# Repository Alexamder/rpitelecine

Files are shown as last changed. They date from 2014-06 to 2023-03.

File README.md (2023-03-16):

# RPi Telecine Project

This project consists of code and models for an 8mm film scanner project based around a Raspberry Pi model B and camera module.
Most of the code is written in Python.

The project is designed to be able to reliably capture each frame of a reel of 8mm film 
(Super 8 or Standard 8) as a high quality photo. Bracketing is possible to cope with underexposed
or dense film.

Once captured, the folder of image files can be transferred to a PC for further processing.

Futher information is available in this Github repository:

* [Description of the electronics](docs/electronics.md)
* [Construction details](docs/mechanics.md)
* [Typical workflow used to digitise films](docs/workflow.md)
* [Hints for post production on a PC](post-production/README.md)
* [Detailed photos available in the images folder](images/)

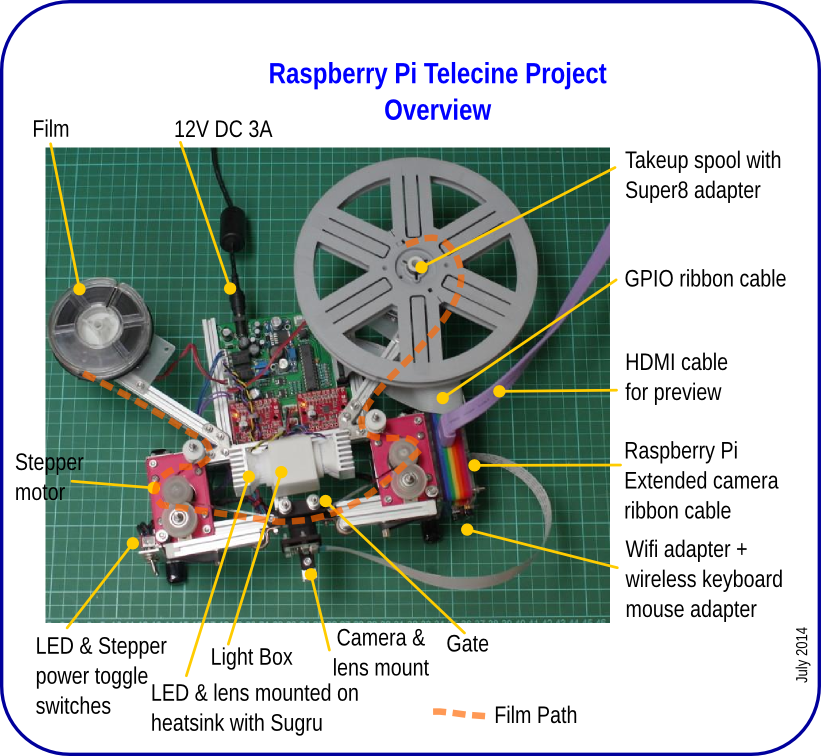
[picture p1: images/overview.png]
Overview of RPI telecine


## Acknowledgements

Thanks to [Raspberry Pi](http://raspberrypi.org) for a splendid little computer and excellent camera module!

Rpi Telecine project design was somewhat inspired by the [Kinograph project](http://kinograph.cc/)

3d printed Gate was inspired [by this design](http://www.mets-telecinesystem.co.uk/index.php/how-its-made/making-the-film-gate).

Chassis makes use of [Makerbeam and accessories](http://www.makerbeam.eu/)

Code makes use of:

* Dave Hughes' [Python picamera library](https://pypi.python.org/pypi/picamera)
* [OpenCV Python bindings](http://opencv.org/)
* Numpy and Scipy

This is a work in progress, and hasn't yet been used on any precious films. It's a good idea to
test using only 'disposable films'. Ebay is a good source of old 'home movies'.

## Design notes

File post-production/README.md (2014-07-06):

# Post-production

These are some simple scripts and snippets of code designed to be run on a full 
power PC, as the Raspberry Pi's ARM processor really isn't up to the job of 
transcoding and processing the large number of images into video. 

My PC runs OpenSUSE Linux with an i5 Processor, and some of the routines take a 
long time.

There are lots of potential processing options, using Linux, OSX or Windows. 
On Linux Openshot and Kdenlive are very good video editors.

## Getting the images onto the PC

Copy the files to from the Pi to the PC. 50 feet of film generates about 5-6GB 
of png files, so it's probably quicker to shut down the Pi, remove the SD card, and
copy the files using an SD card reader on the host PC.  If time isn't an issue, or
you want to keep the Pi running, it's possible to use scp to copy the files over.
As the pictures are stored on the SD card which uses the Ext4 filesystem, you won't be
able to read the card directly on a Windows system without loading additional software.

## Copy files using scp

From the PC, in a terminal:  

```
mkdir <jobname>
cd <jobname>
scp pi@<IP address of Pi>:/home/pi/rpitelecine/<jobname>/*png
```

Replace the job name with the one you chose, and the IP address of the Pi on your 
network. This of course assumes you have set up the ssh server on your Pi. It is possible
to get a work-in-progress copy while the telecine is running a job, but while the
copy is running, the speed of the telecine job halves.

The scp line would be something like:

```
scp pi@192.168.0.13:/home/pi/rpitelecine/familyfilm1/*png
```

With the Pi set up wirelessly, each image takes a second or so to copy. It is quicker to copy 
from the SD card directly, if you are running Linux on the PC. Bear in
mind you are copying about 3,500 pictures for a 50 foot reel of film.

## Create an MP4 film of the video using mencoder

A quick and dirty way of getting video from all the pictures is to use mencoder on
the command line. It's part of mplayer, and should be installed when you installed that
program. I have successfully used this command line:

```
mencoder -nosound -ovc lavc -lavcopts vcodec=mpeg4:mbd=2:trell:autoaspect:vqscale=3 -vf scale=1024:768 -mf type=png:fps=18 mf://img*.png -o <name>.avi
```

Replace <name> at the end with the name of the video you want to create.
You may also want to adjust the framerate after the =fps option - for Super 8 film it
should be 18 frames per second, for standard 8mm it should be 16. Though you may need to 
adjust. Super 8mm with sound is likely to have been shot at 24fps, and older film may be
shot at slower than 16fps...

Digital video players I have tried on the PC, media player hardware, and youtube doesn't 
seem to have trouble with the odd framerate, so it isn't necessary to interpolate frames, 
or alter the rate unless you wish to output to a media like DVD with a fixed 25fps format.

# Use enfuse for combining bracketed pictures

Enfuse is part of Hugin - and is a command line utility that can combine two or more
pictures of the same scene taken with different exposures. [Details here](http://enblend.sourceforge.net/)

Film has a wider dynamic range than is available with the Raspberry Pi camera, so in 
some circumstances it is useful to take two (or possibly more) picturs of the film frame
in order to get as much detail out of it as possible - this is especially true with underexposed
film, or in scenes with a lot of shadow. Some scenes benefit more than others with this
processing, so it may be better to process the normal exmposures as well, and combine
the best scenes using a video editor.

Enfuse can be used to simply combine bracketed sequences pictures using this Python script:

```python
import glob
import os
import subprocess

brackets = 2
name_template = 'img-?????-?'
fmt = '.png'
out_prefix = 'frame-'

files=sorted(glob.glob(name_template + fmt))
n_frames =  len(files)/brackets
FNULL = open(os.devnull, 'w')

processes = 4	# Optimise for number of cores - 4 works well on my i5
counter = 0
while files:
    frame1 = files.pop(0)
    frame2 = files.pop(0)
    outfile = out_prefix + frame1[4:9] + fmt
    print('{}+{} -> {}'.format(frame1,frame2,outfile))
    counter += 1
    cmd = ['enfuse', '-v0', frame1, frame2, '-o', outfile ]
    if counter % processes == 0:
        # Wait until this one finishes
        subprocess.call( cmd, stdout=FNULL, stderr=subprocess.STDOUT)
    else:
        # run in background
        subprocess.Popen( cmd, stdout=FNULL, stderr=subprocess.STDOUT )
```
It very simply goes through all the frames in a sequence, and combines pairs with matching
sequence numbers, creating a new sequence. Enfuse runs slowly, about 1 a second even on my 
Core i5 - but as it only uses a single core on the processor, this script backgrounds 3 of every four, so in
effect running four times faster than simply doing one at a time.

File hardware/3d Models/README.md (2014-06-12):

RPi Telecine Project 3D Models
==============================

These models were created using Freecad parametric design, using v0.14
unstable version. http://freecadweb.org/

STL files were exported and printed using [Shapeways](http://www.shapeways.com/) and 
[3dPrintuk](http://www.3dprint-uk.co.uk/). Film transport rollers were printed using
Shapeways' frosted detail plastic. Seems to work better than Nylon. The gate and camera
mount were printed using Shapeways black nylon. Other parts were standard white nylon.

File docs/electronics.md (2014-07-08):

# RPi Telecine Electronics

## The PCB

The PCB design is pretty simple and comprises the following sections:

* 12V input
* Connectors for 5V regulator for Raspberry Pi and DC motors
* MCP23S17 12 bit IO chip connected to Raspberry Pi SPI port
* 2 x XPPower LED Driver modules + filter and control voltage circuitry
* Headers for 2 x Big Easy Driver stepper motor controllers
* Optically isolated shutter release for external camera
* Mosfet switches for power to 2 x DC motors + LED light
* 5 x GPIO header for unused bits on MCP23S17
* Headers for toggle switches for power to LEDs + Stepper motors
* Headers for 2x power LEDs, 2x DC motors, 2x 4wire stepper motors
* 26way header for Raspberry Pi GPIO port

The PCB is 10cm x 10cm, and is designed to connect to the Pi with a ribbon 
cable. It might be possible to connect it directly to the Pi - but a spacer 
may be required to clear the Pi's ethernet port, and allow space for the camera 
ribbon cable.

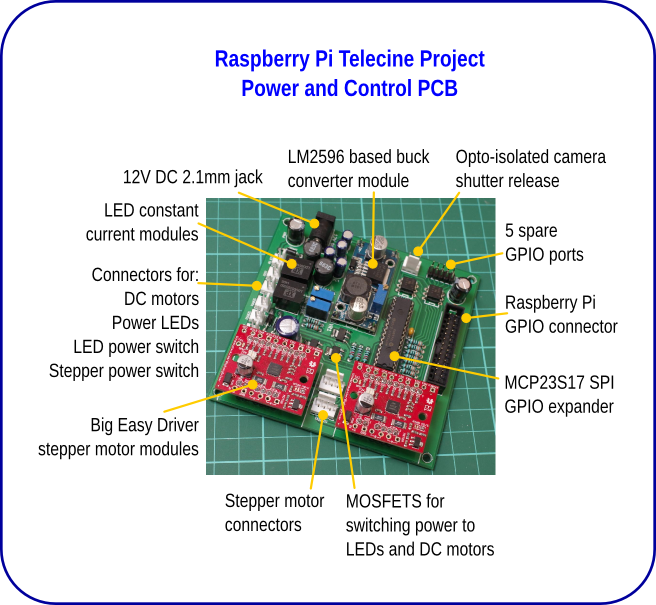
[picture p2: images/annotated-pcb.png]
PCB overview


It is a pretty simple circuit - all through hole components, except for three 
power Mosfets. It uses modules for the 5V power regulator, LED drivers, and 
stepper motors. Power is designed to be provided by a 12V supply, rated at 3A+,
that uses a standard 2.1mm DC jack plug.

5V is provided by an inexpensive LM2596 based module, soldered to headers on 
the PCB. It's also possible to use an alternative buck converter using the pads 
for an alternative header. It's important to use a module that can cope with 2A 
output. I found one of the two LM2596 modules I bought dropped the voltage too 
much when the DC motors were powered, causing the Pi to reboot. Not good. The 
other one works fine. On the prototype I also used a hacked 2A rated car-USB
adapter.

The Raspberry Pi is powered through the 5V line on the 26way connector, so as 
this avoiding the protection on the Pi, it is very important to check the 
voltage provided by the regulator so that it exactly outputs 5V. These modules 
can be set to output anything from 1 - 12V. Adjust the trimmer to the correct 
voltage before connecting the Pi.

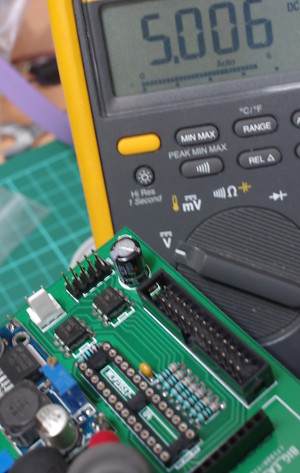
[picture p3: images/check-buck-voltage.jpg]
Check for 5V out of the regulator!

**Very Important**

Using a SPI controlled 16 bit IO expander (the MCP23S17) means that everything 
can be controlled simply using the Python bindings for 
[WiringPi](http://pi.gadgetoid.com/article/wiringpi-version-2-with-extra-python).
It also means that the telecine control scripts can be run as a normal user.

LEDs take advantage of XPPower's LDU05/07/14 Series constant current 
drivers. I have tested with their 700mA, 350mA versions. Details and a link to the 
datasheet are available 
[here](http://uk.farnell.com/xp-power/ldu0516s350/led-driver-dc-dc-cc-0-35a-14v/dp/2082733).
[Datasheet PDF](http://www.xppower.com/pdfs/SF_LDU05-14.pdf) The input filter 
using a 68uH inductor is from the datasheet. The inductors are also available 
[from Farnell](http://uk.farnell.com/murata-power-solutions/13r683c/inductor-68uh-10-1-3a-th-radial/dp/2062695)

The LED drivers also allow for brightness adjustment using a voltage control. I 
implemented this using a trimmer potentiometer and voltage divider.

Stepper motor drivers are 
[Big Easy Stepper drivers](http://www.schmalzhaus.com/BigEasyDriver/) available from 
[Pimoroni](http://shop.pimoroni.com/products/sparkfun-big-easy-driver), 
[Hobbytronics](http://www.hobbytronics.co.uk/big-easy-stepper-driver),
[Sparkfun](https://www.sparkfun.com/products/11876) and other places. They're 
really easy to use, and support 1/16th microstepping, which allows for fine tuning 
of the position of the film. The drivers are plugged into header sockets on the
PCB. It's possible to use screw terminals on the BED boards, or use 2.54mm headers
for the motors. As the BigEasyDriver boards are controlled by 3.3V logic, the 3V/5V 
jumper pad has to be bridged with solder.

Mosfets on the board are the only surface mount components - these are in 
SOT-223 format which is pretty easy to solder. IRLL024NPBF.
[From farnell](http://uk.farnell.com/international-rectifier/irll024npbf/mosfet-n-55v-4-4a-sot-223/dp/8651205?Ntt=8651205)
or cheaper [from CPC](http://cpc.farnell.com/jsp/search/productdetail.jsp?SKU=SC11049) 
These switch the power to the DC motors and for the LED modules. These are logic level
MOSFETS, and are rated to 55V and 4.4A, and require only 2.2V to switch on fully.

Camera release is based around a pair of 4N35 optocouplers. With a 2.5mm jack it can
be used for Canon and Pentax DSLRs. Might also be suitable for other cameras. The 
optocouplers isolate the camera circuit from the Pi. This isn't used for my current
project, but means the PCB is versatile, so could be used with an DSLR like the 
original Kinograph system - or allows the PCB to be used as a timelapse controller.

PCB was designed in Kicad, and I created modules and footprints for the 
BigEasyDrivers, LED drivers and DC module. It was made by Smart-Prototyping, as 
they were having  a special offer on 10x10cm boards.

[Kicad project files are here](../hardware/RPI telecine circuit.zip).

[Gerbers for the PCB are here](../hardware/Gerbers.zip).

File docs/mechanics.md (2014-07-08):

# RPi Telecine construction

## Chassis

The chassis is constructed mainly from [Makerbeam](http://www.makerbeam.eu/) 
10mm extruded aluminium, and associated accessories. The Nema 17 stepper 
motors use the Makerbeam metal bracket, and the servo motors use the lasercut
acrylic servo mount. Arms for the pinch rollers are attached using the
bearing mounts, and the PCB slots between two 10cm beams. The Raspberry Pi in a
Pibow case is attached to the front beam with long steel M3 screws in place
of the standard nylon ones. A long camera ribbon cable goes from the Pi to the
camera.

## 3d printed parts

Various parts in the telecine were 3d printed. A fair amount of precision is required for the 
film handling. It's important that the film path is pretty level - from film-spool to motor 
to gate to motor to take-up spool. 
[Shapeways](http://www.shapeways.com/) and [3dPrintUK](http://www.3dprint-uk.co.uk/)
were used. Shapeways offer a variety of materials and colours, and 3dPrintUK are slightly 
faster and cheaper for larger items - but only in white nylon.

Parts were designed in [Freecad](http://freecadweb.org/), and STL files were sent to
the 3d printing service. Freecad allows designs to be made based on cross-sectional
drawings, and results have been very good.

* Film Gate
* Pi camera mount
* Film roller on stepper motor
* Pinch roller
* Film Idler rollers
* Spool tables
* Light box
* Makerbeam end-stop (protects rubber band)

The film rollers and pinch rollers were printed in Shapeways' frosted detail plastic,
as this gives a good smooth surface for gripping the film edges. First version in 
white standard nylon slipped more. The pinch rollers use bearing races so they can rotate
freely. The film rollers fit steppers with a 5mm D shaped shaft. A little bit of electrical 
tape was used on the shaft to make a tight fit.

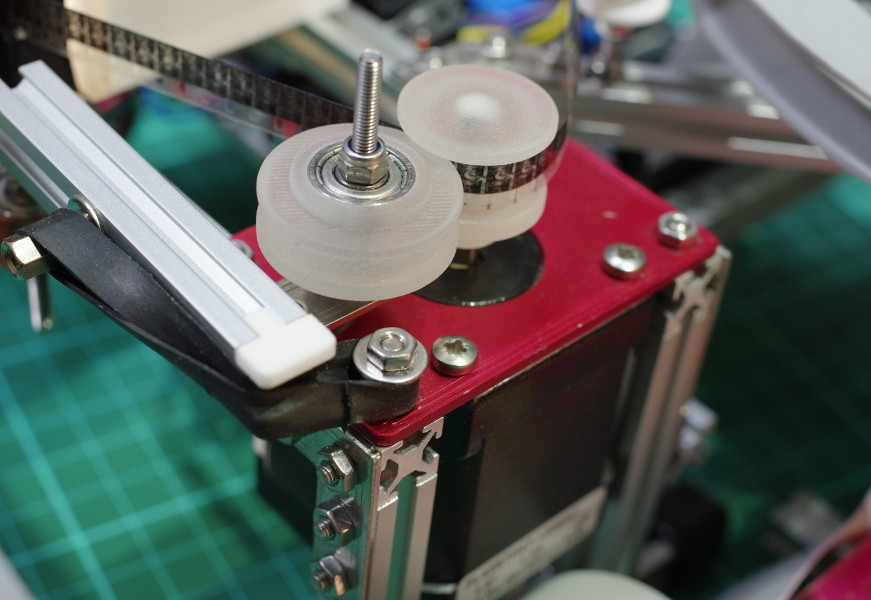
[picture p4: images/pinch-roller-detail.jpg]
Pinch roller detail


Pinch rollers are mounted on swinging arms, and use rubber bands made from an old bicycle 
inner tube to hold the roller in tension with the motor mounted (capstan) roller.
The arms can be released in order to remove the film.

The light box serves to mix the colours of the white and turquoise LEDs, and to diffuse the
light to create a flat area of illumination behind the gate.
The gate and camera mount fit into the slots on the Makerbeam - allowing adustment while
keeping alignment straight.

[Original 3d models and STL files are here](../hardware/3d Models/).

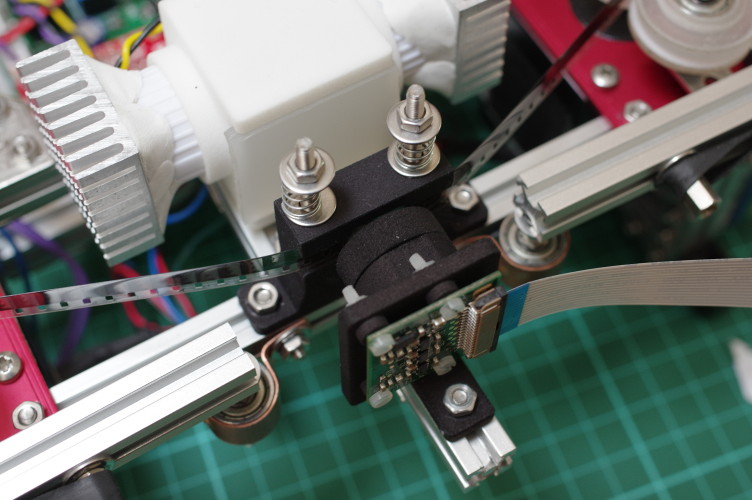
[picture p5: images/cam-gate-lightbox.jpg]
Camera gate and lightbox - 3d printed

3d printed lightbox, gate and camera/lens-mount in situ

## Hacked servos

The film spool tables are attached directly to the splines of the servos. The servos
are standard inexpensive TowerPro MG995s (or copies), but modded for continuous
rotation by pulling out a metal pin that stops the gears rotating 360 degrees, and 
removing the feedback potentiometer. The control PCB was also removed, and two wires
soldered directly to the motor - effectively turning the servo into a compact
simple geared motor. There are various instructions dotted around the net for this
process.

The advantage of using servos is the simplicity of attaching the spool table - it just
uses a single m3 screw, and holds extremely securely. However any DC motor would be suitable.
Film spools are not fixed on the tables - they are designed to rotate freely so film can
be pulled off the reel, and the take-up spool rotates with a little bit of friction, rotating
enough to take up the slack. The motors are designed just to rotate in one direction - in order 
to pull the film onto the spool. 

## Camera and Lens

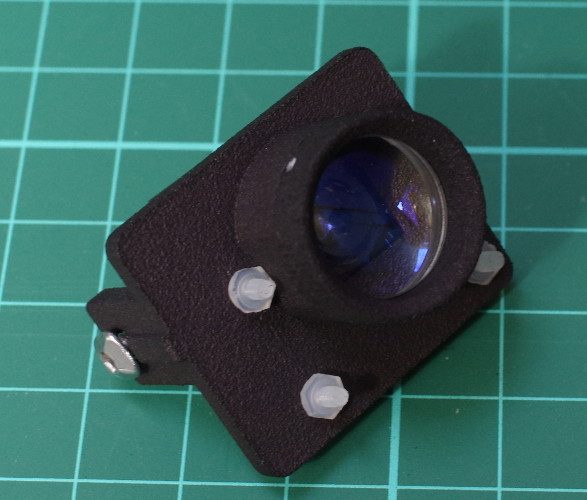
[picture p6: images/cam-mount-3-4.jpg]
Camera and lens assembly


The camera is screwed onto a 3d printed bracket which fits into the slot in a short piece of Makerbeam.
It can be fixed securely, but allows for adjustment and focusing the image. 
To focus closer the Raspberry Pi camera's lens needs to be carefully unscrewed almost
as far as it can. This is not enough to get an 8mm frame large enough in the frame, so an additional
lens is required. 

The first version of the camera mount allowed fixing of a simple
(and inexpensive) smartphone close-up/macro lens. These can be got for cheap from Ebay.
Results using this lens was just about acceptable - the centre of the frame was
pretty sharp, but got softer away from the centre with a fair amount of colour fringing. My 
first examples on Youtube use this lens. Not bad for a lens that costs less than a fiver.

Much better is its replacement - a coated Steinheil triplet, available for a reasonable price from
[Surplus Shed](http://www.surplusshed.com/pages/item/pl1033.html) in the USA. This lens is much sharper
with little chromatic abberation and has less distortion than the smartphone lens. 
It was suggested for macro use by rkinch [in this thread on the Pi forums](http://www.raspberrypi.org/forums/viewtopic.php?f=43&t=43985&start=52).
The camera mount design was adjusted for this lens.

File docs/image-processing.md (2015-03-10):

#Capturing flow

##Image capture

The Pi camera takes a full 5MP image and returns a BGR 8bit image
as an OpenCV compatible Numpy array. A full image capture takes about
0.7 seconds before the data is available. 

##Perforation detection

Perforation detection uses a region of interest - a small part of the whole image
in one channel in order to minimise the amount of processing required.

The perforation will be the largest, brightest area in the ROI image. A vertical 
slice of the ROI is made, and the median value of each row is used to make a 
single column representation of the brightness of the width. This column is
thresholded to create a binary array, and the position of the top and bottom
edge of the perforation is established.

Using a median value across the width of the perforation allows for damaged
sprocket holes. This seems to work quite well.

Optionally the same process is repeated for the left hand edge of the perforation
in order to compensate for horizontal weaving.

The output of the detection is the centre point of the perforation in the image.

##Cropping

The centre point established by the perforation detection is used to calculate
the slice used to crop the film frame from the whole image.

The crop is specified by an offset from the centre point, and its width and 
height. A slice object is created, and the sliced image is sent to the writing
queue.

##Writing

The cut-out frames are placed in a queue with the filename/frame number where 
they are taken by a separate thread and output to SD card or other storage. 
Writing the image data is time consuming. Depending on the size of the image
crop and file format, output is typically 0.8 to 1.5 seconds per frame with
a Raspberry Pi 2 and a reasonably fast Micro-SD card.
 
Using a separate thread to write the images means that the image writing works 
in parallel with moving the film to the next frame, and waiting for the camera
to take the next picture.

##Speed considerations

50 feet of 8mm film has around 3600 frames.
The Pi camera requires 0.7 seconds to set up the camera and take a 5MP still
picture and get the RGB data for further analysis and processing.
The other time consuming process is the saving of the cropped image. A crop that is
about 1800x1300 pixels large takes about 0.9 seconds to write as a 620K JPG, or 
1.4 seconds to write a 3.3MB PNG. 

Experiments have shown that OpenCV is the fastest at saving of images. I have
tried using PIL and Qt, and the PNG save takes in excess of 3-4 seconds. So
it's back to using OpenCV.

Total job time is therefore determined by either the picture taking, or the
image saving elements of the process - whichever is longest.

At present, it doesn't seem possible to increase the speed of the camera. In 
order to get the consistent exposure needed by the telecine, the stills 
port is required. My attemps at trying to get full resolution images using
the Pi's video port have failed. It would be nice to be able to get
multiple images per second out of the camera.

It may be possible to use multiple threads to write the data files - but
this will be limited by the maximum IO speed, either over the USB if 
saving to an external drive, or using the SD card interface. JPEG and PNG
compression require quite a lot of processing power, so it might be beneficial
to have the writing threads on separate processor cores.

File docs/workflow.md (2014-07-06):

# Workflow for a telecine job

This is the basic workflow to convert a film. It's mainly designed for the Pi
to run headless while doing the capture. The setup routine uses a GUI of sorts - 
basically shows a preview of the crop settings, but it is mainly keyboard
controlled.

## Set base exposure

If base whitebalance/shutter speed hasn't been set, or if lighting
has been altered:

1. Without film in gate, put a neutral density filter in front of lamp diffuser
2. Run tc-setwhitebalance.py to set base exposure and white balance

## Set up telecine job

1. Lace the film and pull it through the gate manually. If possible move it to a frame.
2. Run tc-setupjob.py [-b|--brackets] [-s8|--standard8] <jobname>
3. Click in a sprocket hole to set up frame detection
4. Calibrate the transport - press the # key - or do each step individually with u|t|y
5. Use '[' and ']' keys to jump forward or back; or ','/'.' to move one frame forward, back
6. Adjust the crop with arrow keys and PgUp/PgDn
7. Adjust the exposure (+/-) and red/blue gains (rR & bB). Toggle greyscale with g. Toggle clipping with 'c'
8. Use transport keys to move the film to the first frame in the job.
9. Save settings to job ini file with s. To exit without saving use Esc.

The preview can be used to check focus, exposure, etc. It's slow, but just about 
usable over a remote X connection (via ssh).

## Run job

1. Run tc-run.py jobname -s start-frame -e end-frame [-j] [-r] [-b]

'-j' option saves images to jpeg. '-r' runs the transport backwards. '-b' forces bracketing.
Start frame and end frame numbers are inclusive. The tc.run.py runs in the console,
so you can use the screen command to run in the background and headless. 

5 consecutive failures to detect a perforation will stop the job. This is usually at
the end of the reel - or if there's some damage on the film.

All frames will be saved to a sub folder named after the job name. Failed 
perforation detections will be saved as full frames as well as cropped, so they
can be cropped manually if necessary.

## Keys in setup routine

| Keys | Description |
| --- | --- |
| s | Save current settings |
| Esc	 | Escape without saving |
| c	 | Toggle clipped colours |
| g	 | Toggle grayscale |
| d	 | Cycle through DRC settings (off,low,med,high) |
| - +	 | Reduce / increase shutter |
| r  R	 | Reduce / increase red gain |
| b  B	 | Reduce / increase blue gain |
| p	 | Toggle perforation detection |
| o	 | Centre frame |
| i	 | Redetect perforation |
| #	 | Calibrate Transport (same as u/t/y) |
| t  y	 | Calibrate transport forward/backward |
| u	 | Calibrate pixels per motor step |
| .  ,	 | Previous / next frame |
| <  >	 | Back or forwards 18 frames |
| [  ]	 | Fast wind back / forward 18 frames |
| {  }	 | Fast wind back / forward 180 frames |
| Arrows | Move crop |
| PgUp	 | Make crop larger |
| PgDn	 | Make crop smaller |
| Home	 | Nudge motor forward |
| End	 | Nudge motor backward |
| 1-4	 | Display reduction (1 full size, 4 quarter size) |

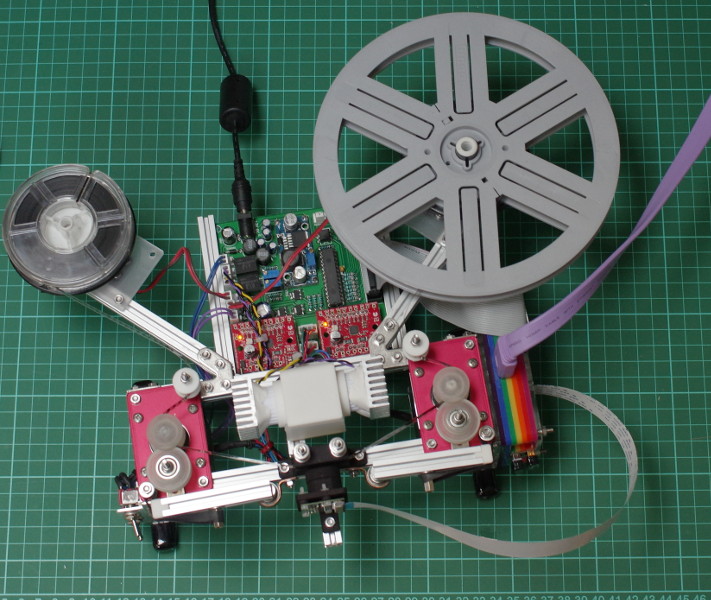
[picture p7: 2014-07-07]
images/rpi-telecine-overview.jpg

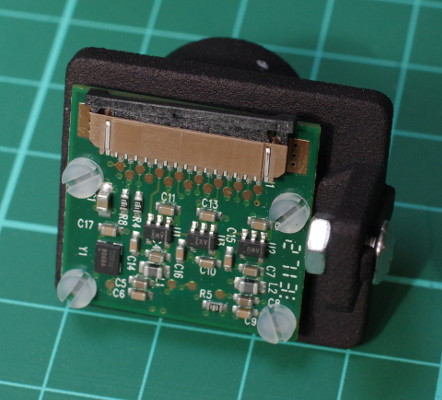
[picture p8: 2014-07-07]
images/cam-mount-3-5.jpg

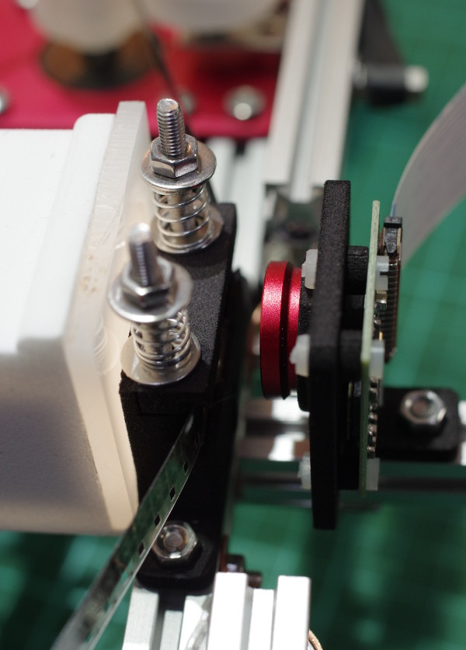
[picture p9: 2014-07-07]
images/orig-lightbox-lens.jpg

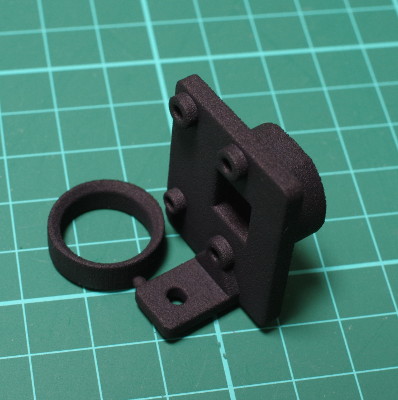
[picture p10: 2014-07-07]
images/cam-mount-3-1.jpg

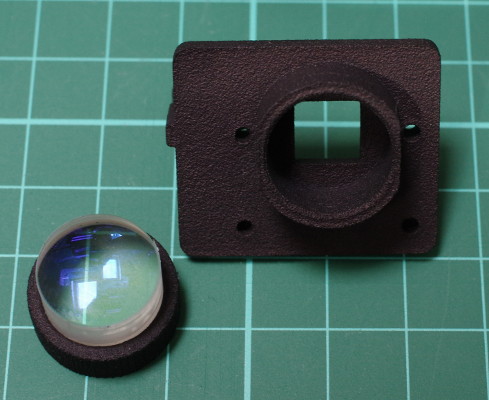
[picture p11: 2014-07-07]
images/cam-mount-3-3.jpg

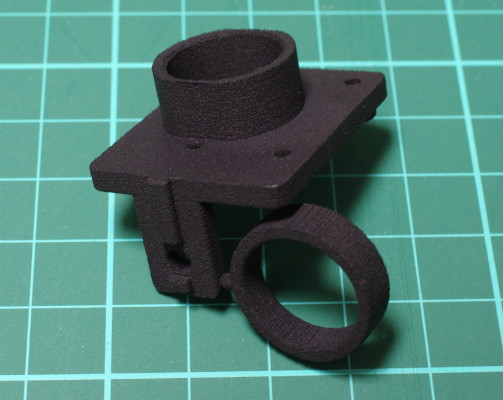
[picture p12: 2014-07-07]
images/cam-mount-3-2.jpg

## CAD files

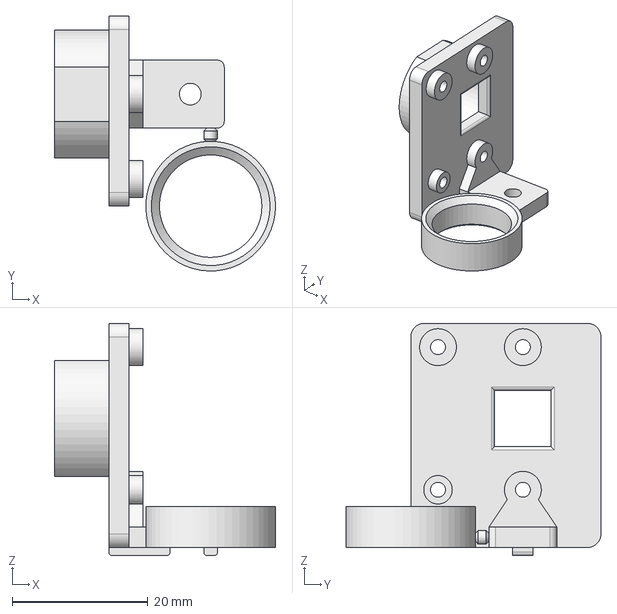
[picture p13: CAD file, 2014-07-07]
hardware/3d Models/camera-mount-3.fcstd
32.6 x 37.5 x 34.2 mm

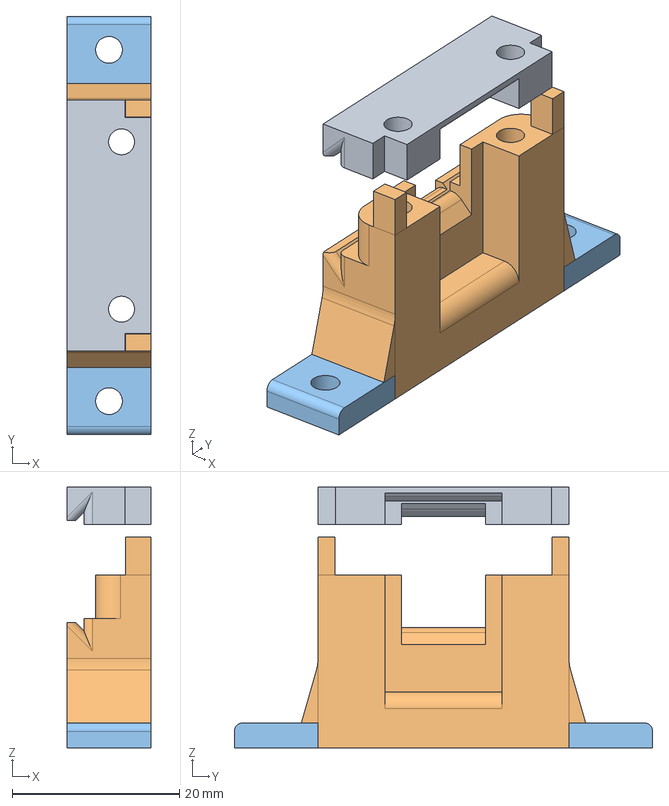
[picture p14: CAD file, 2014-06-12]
hardware/3d Models/gate2.fcstd
10.0 x 50.0 x 31.2 mm

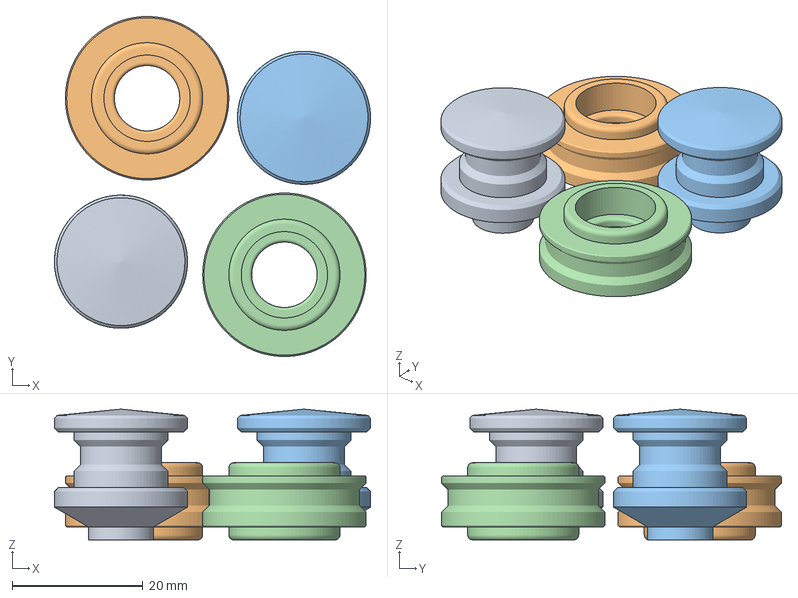
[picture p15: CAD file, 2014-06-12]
hardware/3d Models/rollers-2.fcstd
48.4 x 52.0 x 20.0 mm
motor-roller
pinch-roller
motor-roller001
pinch-roller001

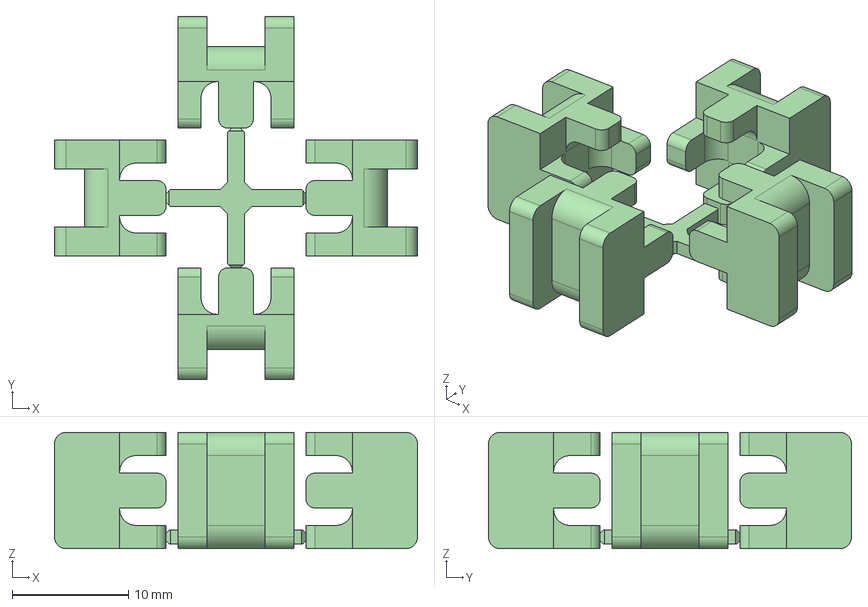
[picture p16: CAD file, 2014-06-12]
hardware/3d Models/beam-stop.fcstd
31.2 x 31.2 x 10.0 mm
Sprue
Fusion Refined

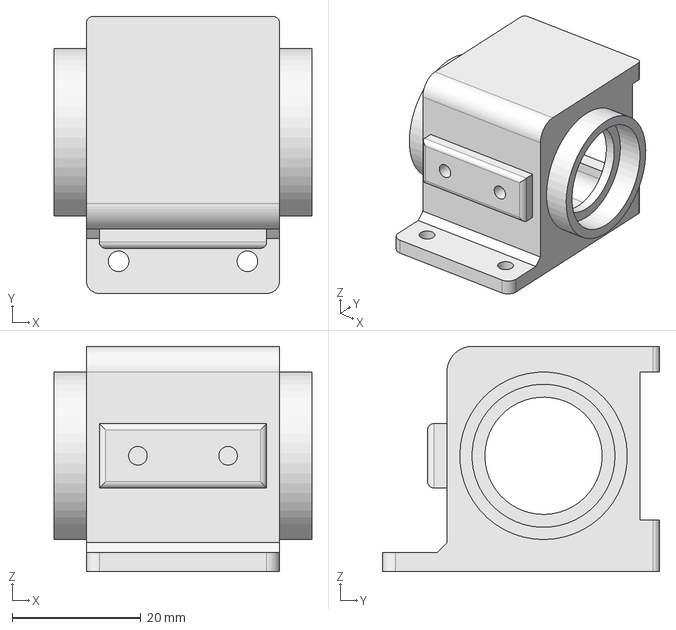
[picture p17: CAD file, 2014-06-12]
hardware/3d Models/lightbox2.fcstd
40.0 x 43.0 x 35.0 mm

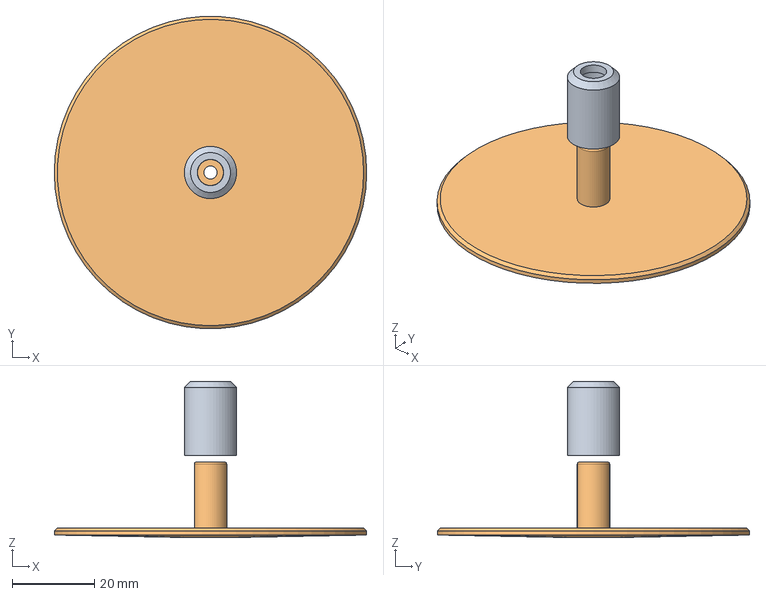
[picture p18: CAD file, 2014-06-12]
hardware/3d Models/film-table.fcstd
75.9 x 75.8 x 38.0 mm
Super8 Adapter
Film Table

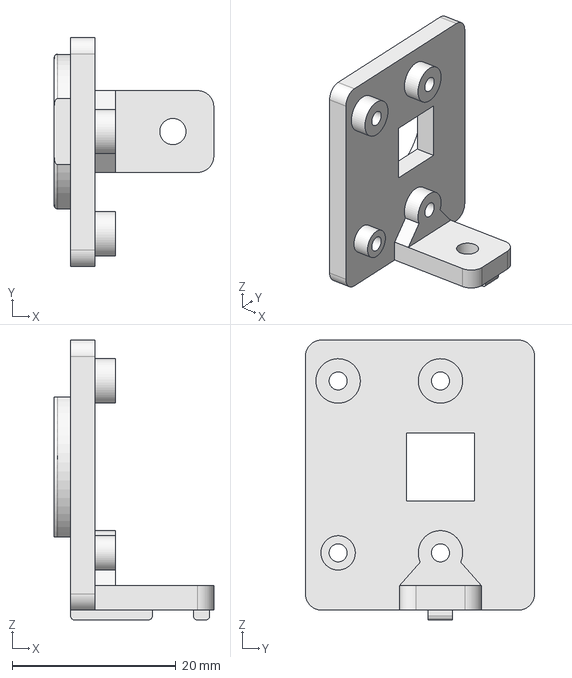
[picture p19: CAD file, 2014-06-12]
hardware/3d Models/camera-mount.fcstd
19.5 x 28.0 x 34.2 mm

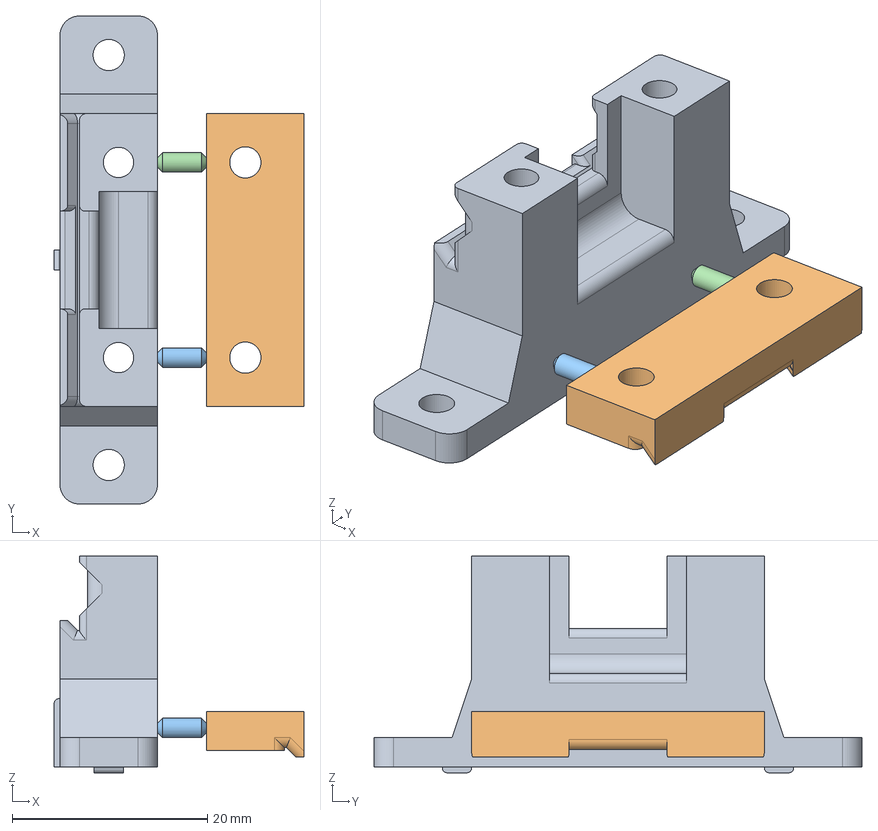
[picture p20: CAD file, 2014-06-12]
hardware/3d Models/gate3.fcstd
25.6 x 50.0 x 22.2 mm
Body001 (Solid)
Top002 (Solid)

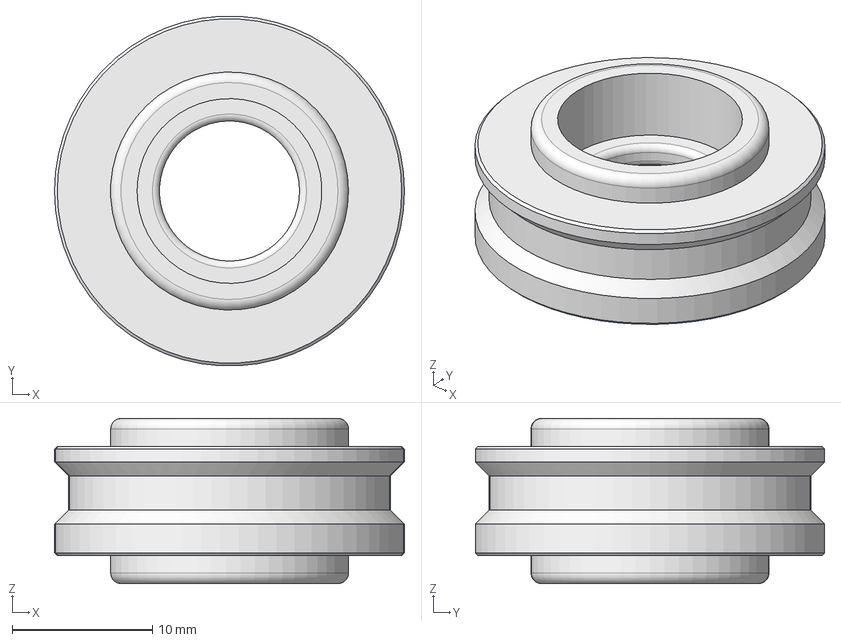
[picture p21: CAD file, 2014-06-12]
hardware/3d Models/pinch-roller.fcstd
25.0 x 25.0 x 11.8 mm

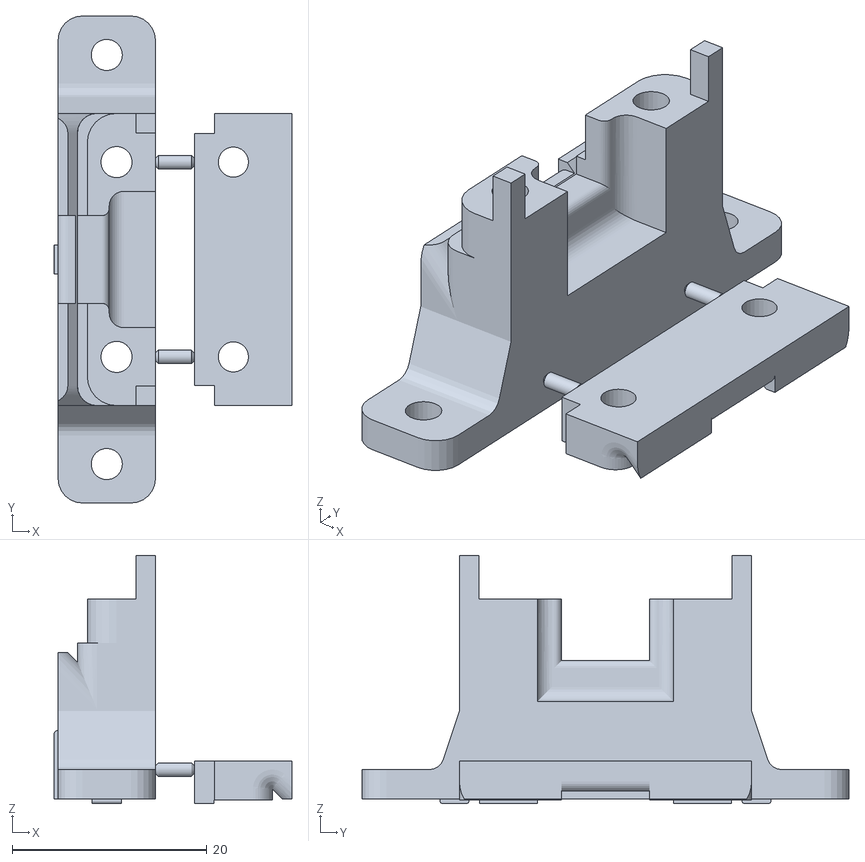
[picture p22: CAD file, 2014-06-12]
hardware/3d Models/gate.stl
24.4 x 50.0 x 25.5

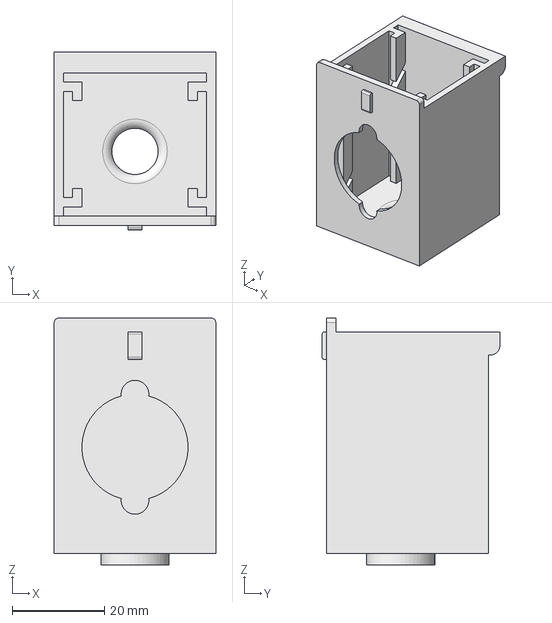
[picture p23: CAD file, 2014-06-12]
hardware/3d Models/light-box.fcstd
35.0 x 38.5 x 53.5 mm

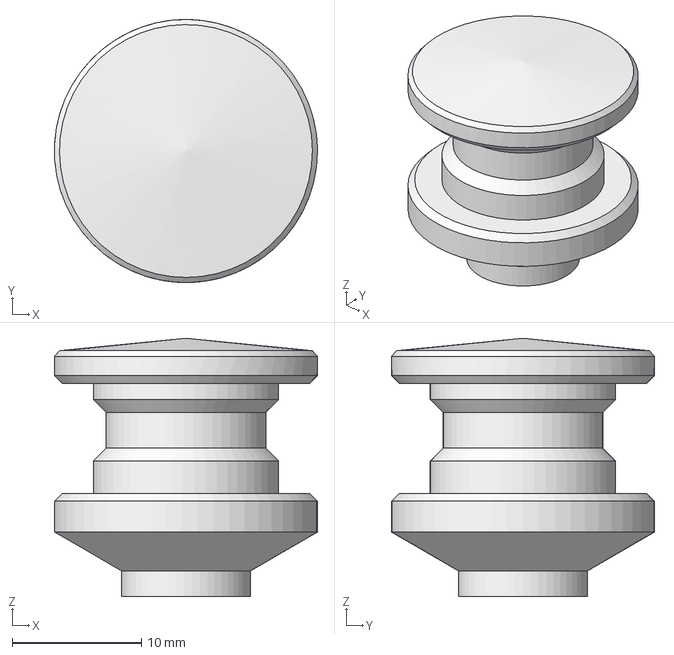
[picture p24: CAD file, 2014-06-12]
hardware/3d Models/motor-roller.fcstd
20.3 x 20.4 x 20.0 mm

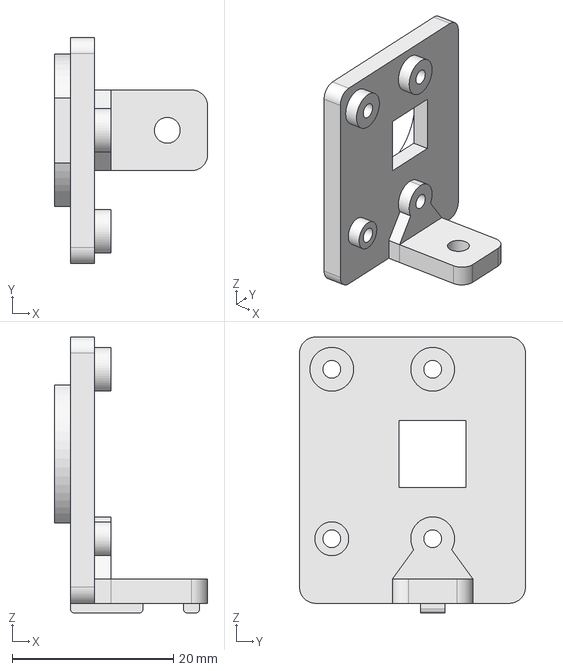
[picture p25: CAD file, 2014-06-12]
hardware/3d Models/camera-mount-2.fcstd
19.0 x 28.0 x 34.2 mm

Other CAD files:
hardware/3d Models/beam-stop.stl
hardware/3d Models/camera-mount2.stl
hardware/3d Models/camera-mount3.stl
hardware/3d Models/gate3.stl
hardware/3d Models/light-box2.stl
hardware/3d Models/rollers2.stl

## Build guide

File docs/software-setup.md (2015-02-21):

# Setting up the rpiTelecine software

These are the steps required to get the Python scripts working with my 
telecine hardware. I am currently using a Raspberry Pi B version 2 - as the telecine 
processing really benefits from additional memory and the extra processor cores.
These instructions were tested using NOOBS 1.4.0 released on 18 February 2015.
A main prerequisite is the Python-picamera library, which is installed by default with
the current version of Raspbian. Other prerequisites are WiringPi2, WiringPi2-Python and OpenCV.

## Download and install NOOBS

Get the latest version from http://www.raspberrypi.org/downloads/
Copy it on a good fast Micro-SD card as per the directions on the Raspberry Pi web site. 
Boot your fresh SD card and install Raspbian.

## raspi-config

When the Pi reboots, various settings are required in raspi-config which runs when the system
starts for the first time. These settings can be done at any time by entering the following at the command line:
```
$ sudo raspi-config
```

* 2 Change user password - it's always a good idea. Make a note of it.
* 5 Enable Camera

The rest of the settings are in the Advanced section:

* A3 Memory Split - Set to 192MB. For full resolution stills, Python picamera requires the GPU to have more RAM than the default
* A4 SSH - Enable SSH if you use SSH to connect to the Pi, or to transfer files from it
* A6 SPI - Enable SPI, and set the kernel module to load by default

Reboot the Pi

## Set up network

Plug in a network cable, or set up the wireless network adapter.
For the latter, the easiest way is to go into LXDE with 'startx' and click Menu->Preferences->WiFi Configuration

## Update and install packages
Python-dev and python-setuptools are used to install wiringPi2; OpenCV is used in the rpiTelecine scripts 
to provide a rudimentary GUI and image saving capability, and Scipy is used for some simple image analysis.

```
$ sudo apt-get update
$ sudo apt-get upgrade
$ sudo apt-get install python-dev python-setuptools 
$ sudo apt-get install libopencv-dev python-opencv python-scipy
```

## Install WiringPi2 and WiringPi2-Python

```
$ git clone git://git.drogon.net/wiringPi
$ cd wiringPi 
$ sudo ./build
$ cd 
$ git clone https://github.com/Gadgetoid/WiringPi2-Python.git
$ cd WiringPi2-Python
$ sudo python setup.py install
$ cd
```

## Install rpiTelecine scripts from Github

```
$ git clone https://github.com/jas8mm/rpiTelecine.git
$ cd rpiTelecine
```

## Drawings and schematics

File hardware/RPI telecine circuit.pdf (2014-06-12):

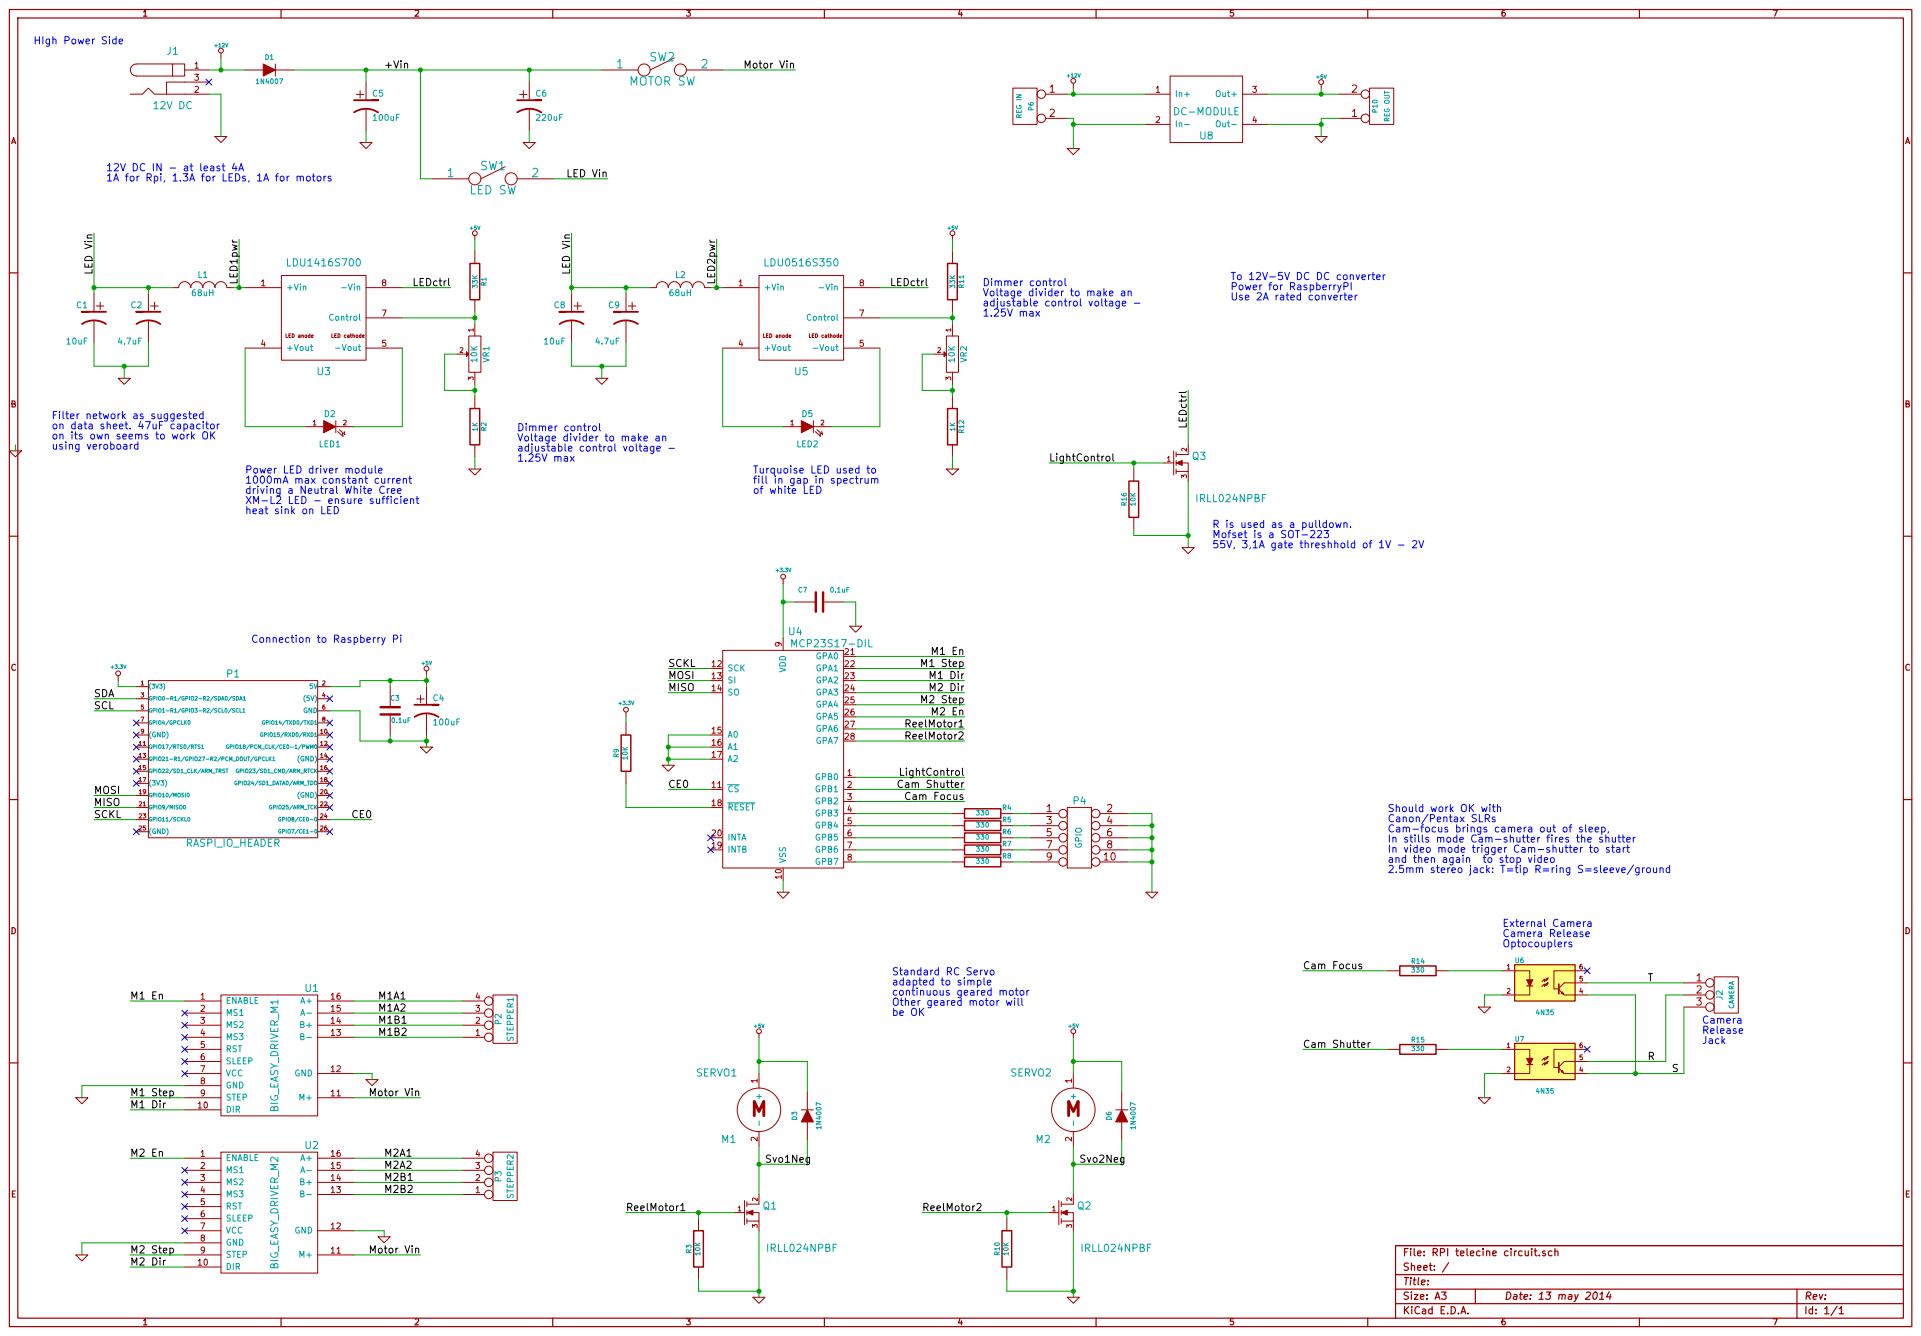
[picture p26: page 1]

+12V M1 Step M1 Dir M1 En M2 En M2 Dir M2 Step

Power for RaspberryPI Use 2A rated converter 12V DC IN - at least 4A
1A for Rpi, 1.3A for LEDs, 1A for motors

To 12V-5V DC DC converter

adjustable control voltage - 1.25V max

adjustable control voltage - 1.25V max Filter network as suggested
on data sheet. 47uF capacitor
on its own seems to work OK

Turquoise LED used to
fill in gap in spectrum
of white LED

1000mA max constant current driving a Neutral White Cree XM-L2 LED - ensure sufficient heat sink on LED

Connection to Raspberry Pi

Jack Should work OK with
Canon/Pentax SLRs
Cam-focus brings camera out of sleep,
In stills mode Cam-shutter fires the shutter
In video mode trigger Cam-shutter to start
and then again to stop video
2.5mm stereo jack: T=tip R=ring S=sleeve/ground

IRLL024NPBF Standard RC Servo
adapted to simple
continuous geared motor
Other geared motor will

Id: 1/1 Title: File: RPI telecine circuit.sch Sheet: /

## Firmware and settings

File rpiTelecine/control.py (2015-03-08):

# RPi Telecine - Controller board 
#
# Code to encapsulate the operation of the controller board
#	
# The telecine board uses an MCP23S17 digital IO expander to control:
# 	2x stepper motors in microstepping mode using  BigEasyDriver modules
# 	2x geared motors for film reel takeup
# 	Power LED to illuminate film
# 	External camera shutter release circuit using 2 opto-couplers.
# 	Remaining pins on the MCP23S17 are broken out for future use and
# 	can be used as GPIOs
# 	
# Version 1 of the PCB is 10x10cm with pin headers for the motors,
# 2 x power LEDs, Raspberry Pi model B and GPIO. Wiringpi2 is used
# for control. The PCB takes a 3A+ 12V power supply, and provides
# power for the Pi using the 5V pin of the Pi's GPIO header.
# For the two power LEDs, XPPower LDU0516S350 (or similar with
# identical pinout) are used. These allow a control voltage to
# adjust the brightness - so they can be trimmed on the board. 
# The PCB uses a LM2596 adjustable buck converter (Check that it
# outputs 5V before connecting the Pi!), and Big Easy Drivers for the
# stepper motors. The BEDs, although expensive, allow the microstepping
# required for the film transport.
# The LED power and DC motors are switched using Mosfets.
#
# Prerequisites: 
#   Wiringpi2 for Python
#   SPI needs to be enabled from raspi-config so the correct kernel 
#   modules are loaded on boot.
#
# Copyright (c) 2014, Jason Lane
# 
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
# 3. Neither the name of the copyright holder nor the names of its contributors 
# may be used to endorse or promote products derived from this software without 
# specific prior written permission.

# THIS SOFTWARE IS PROVIDED BY THE COPYRIGHT HOLDERS AND CONTRIBUTORS "AS IS" AND 
# ANY EXPRESS OR IMPLIED WARRANTIES, INCLUDING, BUT NOT LIMITED TO, THE IMPLIED 
# WARRANTIES OF MERCHANTABILITY AND FITNESS FOR A PARTICULAR PURPOSE ARE 
# DISCLAIMED. IN NO EVENT SHALL THE COPYRIGHT HOLDER OR CONTRIBUTORS BE LIABLE FOR 
# ANY DIRECT, INDIRECT, INCIDENTAL, SPECIAL, EXEMPLARY, OR CONSEQUENTIAL DAMAGES 
# (INCLUDING, BUT NOT LIMITED TO, PROCUREMENT OF SUBSTITUTE GOODS OR SERVICES; 
# LOSS OF USE, DATA, OR PROFITS; OR BUSINESS INTERRUPTION) HOWEVER CAUSED AND ON 
# ANY THEORY OF LIABILITY, WHETHER IN CONTRACT, STRICT LIABILITY, OR TORT 
# (INCLUDING NEGLIGENCE OR OTHERWISE) ARISING IN ANY WAY OUT OF THE USE OF THIS 
# SOFTWARE, EVEN IF ADVISED OF THE POSSIBILITY OF SUCH DAMAGE.


from __future__ import division
from wiringpi2 import *

class tcControl():
    
    pin_base=100
    m1_en_pin = pin_base+0
    m1_step_pin = pin_base+1
    m1_dir_pin = pin_base+2
    m2_en_pin = pin_base+5
    m2_step_pin = pin_base+4
    m2_dir_pin = pin_base+3
    reel1_pin = pin_base+6
    reel2_pin = pin_base+7
    led_pin = pin_base+8
    shutter_pin = pin_base+9
    focus_pin = pin_base+10
    gpio1_pin = pin_base+11
    gpio2_pin = pin_base+12
    gpio3_pin = pin_base+13
    gpio4_pin = pin_base+14
    gpio5_pin = pin_base+15
    
    
    # Parameters to pulse takeup reel every so often to keep film
    # wrapped around rollers
    take_up_steps = take_up_counter = 550
    
    # Because of slippage in system skip pushing film every so often
    # Without this, film tends to start to slacken and bunch up
    # before the gate. 
    tension_steps = 50
    step_counter = 0
    
    def __init__(self):
	wiringPiSetupSys()
	mcp23s17Setup(self.pin_base, 0, 0) 
	# Stepper Motors
	self.m1 = stepperMotor(self.m1_step_pin, self.m1_dir_pin, self.m1_en_pin)
	self.m2 = stepperMotor(self.m2_step_pin, self.m2_dir_pin, self.m2_en_pin)
	# DC motors for takeup reels
	self.reel1 = reelMotor(self.reel1_pin)
	self.reel2 = reelMotor(self.reel2_pin)
	# LED control
	self.led = ledControl(self.led_pin)
	# Shutter release
	self.shutter_release = shutterRelease(self.focus_pin, self.shutter_pin)
	self.m1.on()
	self.m2.on()
	# Direction of film travel - 
	# Forward: True = m1 to m2 False = m2 to m1
	self.m1.set_direction(True)
	self.m2.set_direction(True)
	self.direction = True
	
    def light_on(self):
	self.led.on()
	
    def light_off(self):
	self.led.off()
	
    def change_direction( self, d = True ):
	"""
	Set parameters when direction changes
	"""
	self.direction = d
	self.take_up_counter = self.take_up_steps
	self.step_counter = self.tension_steps
	self.m1.set_direction(d)
	self.m2.set_direction(d)

    def steps_forward(self,steps=1):
	""" 
	Take steps forward - pulse the takeup reel and tension film
	by ignoring push step occasionally
	"""
	m1step = self.m1.step	# Speed up loop a bit by not evaluating dots
	m2step = self.m2.step
        if not self.direction:
            self.change_direction( True )
	while steps>1:
            steps -= 1
	    self.take_up_counter -= 1
            if self.take_up_counter==1:
                self.reel2.pulse()
                self.take_up_counter=self.take_up_steps
	    if self.step_counter>0:
		# Push film one step
		m1step()
		self.step_counter -= 1
	    else:
		# Skip pushing
		self.step_counter = self.tension_steps
	    # Pull film one step
	    m2step()
    
    def steps_back(self,steps=1):
	""" 
	Take steps backwards
	"""
	m1step = self.m1.step	# Speed up loop a bit by not evaluating dots
	m2step = self.m2.step
        if self.direction:
            self.change_direction( False )
        while steps>1:
            steps -= 1
	    self.take_up_counter -= 1
	    if self.take_up_counter==0:
                self.reel1.pulse()
                self.take_up_counter=self.take_up_steps
	    if self.step_counter>0:
		m2step()
		self.step_counter -= 1
	    else:
		self.step_counter = self.tension_steps
	    m1step()	


    def tension_film(self,steps=200):
	# Run steppers in opposite direction for a short period - Tightens up the film
	d = self.direction
	self.m1.set_direction(False)
	self.m2.set_direction(True)	
	for n in xrange(steps):
	    self.m1.step()	
	    self.m2.step()	
	self.m1.set_direction(d)
	self.m2.set_direction(d)

    
    def clean_up(self):
	# Switch things off to tidy up
	self.led.off()
	self.reel1.off()
	self.reel2.off()
	self.m1.off()
	self.m2.off()
	
class stepperMotor():
			
    """
    Simple Stepper motor control class

    Simple class to control stepper motors
    using the BigEasyDriver
    http://www.schmalzhaus.com/BigEasyDriver/

    To control one motor these pins are used:

    EN - Enable/Energise the motor (optional)
    DR - Direction of step
    ST - Step
    GND - Ground connection

    Motor is energised by default - the EN pin can switch power to motor 
    off, to allow manual positioning etc. This connection is optional.

    Big Easy Driver defaults to 3200 steps per rotation, microstepping 
    mode. Re-energising the coils after sleeping will set the nearest 
    whole step
    """

    delay = 1 # Big Easy Driver requires a pulse of 1uS or longer.
    motor_on = False
    
    rotation_steps = 3200
    # Big Easy Driver defaults to 3200 steps per 360degree rotation
    # if the motor has 200 steps per 360degree.
    # Change this if your motor is different
    
    def __init__(self,step_pin,dir_pin,en_pin):
        
        self.step_pin = step_pin
        self.dir_pin = dir_pin
        self.en_pin  = en_pin
        pinMode( step_pin, 1 )         # Output
        pinMode( dir_pin, 1 )          # Output
        pinMode( en_pin, 1 )       	# Output
        self.on()
        self.direction = True
             
    def on(self):
        # enable motor - set motorOn flag
        digitalWrite(self.en_pin,False)
        self.motor_on = True
        
    def off(self):
        # if enable pin is used, de-energise the motor coils
        digitalWrite(self.en_pin,True)
        self.motor_on = False

    def set_direction( self,direction=True ):    
	# set Direction of motor - true=ccw; false=cw
	self.direction = 1 if direction else 0
	digitalWrite(self.dir_pin, self.direction)
        
    def step(self):
	# Make a step
	# Big Easy Driver will step when the pin rises
	# Should be on and off for at least 1uS 
	digitalWrite(self.step_pin,True)
	#delayMicroseconds(self.delay)
	digitalWrite(self.step_pin,False)
	#delayMicroseconds(self.delay)
        
    def steps(self,s):
        # Go s steps
        for i in xrange(0,s):
            self.step()
    
    def rotate_full(self):
        # Make a full rotation
        self.steps(self.rotation_steps)
            
    def rotate_half(self):
        # Make a half rotation
        self.steps(self.rotation_steps//2)
     
    def rotate_quarter(self):
        # Make a quarter rotation
        self.steps(self.rotation_steps//4)

class ledControl:
    """
    Simple Class to control the LED power
    """

    def __init__(self,pin):
	self.pin = pin
	pinMode( pin, True )
	self.off()

    def on(self):
	digitalWrite( self.pin, True )

    def off(self):
	digitalWrite( self.pin, False )


class reelMotor:
    """
	Class to control DC motors for film spools
	The motors are controlled simply by switching on a wiringpi pin
    """
    pulse_delay = 35	# Pulse delay in milliseconds

    def __init__(self,pin):
	self.pin = pin
	pinMode( pin, True )
	self.off()

    def on(self):
	digitalWrite( self.pin, True )

    def off(self):
	digitalWrite( self.pin, False )

    def pulse(self):
	digitalWrite( self.pin, True )
	delay( self.pulse_delay )
	digitalWrite( self.pin, False )


class shutterRelease():
    """
    Telecine SLR shutter release class

    Uses 2 pins with wiringPi2 - connected to a pair of opto-couplers
    and a cable to  2.5mm tip/ring/sleeve (stereo) jack used
    by Pentax and some Canon shutter release cables. Will probably
    work in a similar way using a different connector with other 
    cameras. This method is used a lot with Arduinos.
    The delay settings were established by trial and error with my own
    DSLR. There is opten quite a lag for the camera to start and take
    a picture.
    """
    
    wake_delay = 1500  # Delay in ms to wait for camera to wake up
    shutter_delay = 300 # Delay in milliseconds to hold shutter pin high 
    
    def __init__(self,focus_pin, shutter_pin):
        self.focus_pin = focus_pin
        self.shutter_pin = shutter_pin
        pinMode( focus_pin, 1 )          # Output
        pinMode( shutter_pin, 1 )          # Output
        digitalWrite(self.focus_pin,False)
        digitalWrite(self.shutter_pin,False)
        
    def wake_camera(self):
        digitalWrite(self.focus_pin,True)
        delay( self.wake_delay )
        digitalWrite(self.focus_pin,False)
          
    def fire_shutter(self):
        digitalWrite(self.shutter_pin,True)
        delay( self.shutter_delay )
        digitalWrite(self.shutter_pin,False)
        
        
# Test the hardware
if __name__ == '__main__':
    tc =  tcControl()
    tc.light_on()
    for j in range(1,15):
	delay(500)
	tc.steps_forward(310)
    delay(2000)
    for j in range(1,15):
	delay(500)
	tc.steps_back(310)	
    tc.clean_up()
    
	

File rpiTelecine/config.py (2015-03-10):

# RPi Telecine Configuration
#
# Config file handling for the telecine scripts 
# Provides for reading and writing the job's ini file
#
# Copyright (c) 2015, Jason Lane
# 
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
# 3. Neither the name of the copyright holder nor the names of its contributors 
# may be used to endorse or promote products derived from this software without 
# specific prior written permission.

# THIS SOFTWARE IS PROVIDED BY THE COPYRIGHT HOLDERS AND CONTRIBUTORS "AS IS" AND 
# ANY EXPRESS OR IMPLIED WARRANTIES, INCLUDING, BUT NOT LIMITED TO, THE IMPLIED 
# WARRANTIES OF MERCHANTABILITY AND FITNESS FOR A PARTICULAR PURPOSE ARE 
# DISCLAIMED. IN NO EVENT SHALL THE COPYRIGHT HOLDER OR CONTRIBUTORS BE LIABLE FOR 
# ANY DIRECT, INDIRECT, INCIDENTAL, SPECIAL, EXEMPLARY, OR CONSEQUENTIAL DAMAGES 
# (INCLUDING, BUT NOT LIMITED TO, PROCUREMENT OF SUBSTITUTE GOODS OR SERVICES; 
# LOSS OF USE, DATA, OR PROFITS; OR BUSINESS INTERRUPTION) HOWEVER CAUSED AND ON 
# ANY THEORY OF LIABILITY, WHETHER IN CONTRACT, STRICT LIABILITY, OR TORT 
# (INCLUDING NEGLIGENCE OR OTHERWISE) ARISING IN ANY WAY OUT OF THE USE OF THIS 
# SOFTWARE, EVEN IF ADVISED OF THE POSSIBILITY OF SUCH DAMAGE.

from __future__ import division

import os
import ConfigParser



class telecineConfig():
    
    config = ConfigParser.SafeConfigParser()
    film_type = 'super8'

    shutter_speed = 0
    awb_gains = [1.5,1.5]
    show_gray = False
    brackets = False
    
    # Dynamic Range Compression
    drc_values = ('off','low','medium','high')
    drc = 'off'
    # Image Effects - allow a subset of ones known to work with the perf detection
    image_effect_values = ('none','denoise','colorbalance','saturation','washedout',
        'blur','film',  'colorswap','sketch','oilpaint','hatch','pastel','watercolor',\
        'posterise','colorpoint','cartoon')
    image_effect = 'none'
    
    perf_size = [0,0] # Perforation size - w,h
    perf_cx = 0 # Perforation centre line - cx

    # Crop offset size
    crop_offset = [0,0] # Cropping position relative to perf_centre - x_offset, y_offset
    crop_size = [0,0] # Size of crop in pixels - w,h
    ave_steps_fd = 0
    ave_steps_bk = 0
    pixels_per_step = 5

    def __init__(self):
	pass
	 
    def read_configfile(self,job_name):
	if job_name != '':
	    self.job_name = job_name
	    self.configname = job_name + '.ini'
	# Read job config file - so we retain existing settings
	# Get baseline exposure from ~/.telecine.ini
	cnf_file = self.config.read([os.path.expanduser('~/.telecine.ini'),self.configname])
	section = 'Telecine'
	if section not in self.config.sections():
	    self.config.add_section(section)

	options = self.config.options(section)
	if 'film_type' in options:
	    self.film_type = self.config.get(section,'film_type')
	if 'shutter_speed' in options:
	    # Use a previously recorded shutter speed as a baseline
	    self.shutter_speed = self.config.getint(section,'shutter_speed')
	else:
	    self.shutter_speed = 2000
	if 'gain_r' in options:
	    self.awb_gains[0] = self.config.getfloat(section,'gain_r')
	if 'gain_b' in options:
	    self.awb_gains[1] = self.config.getfloat(section,'gain_b')
	if 'perf_w' in options:
	    self.perf_size[0] = self.config.getint(section, 'perf_w')
	if 'perf_h' in options:
	    self.perf_size[1] = self.config.getint(section, 'perf_h')
	if 'perf_cx' in options:
	    self.perf_cx = self.config.getint(section, 'perf_cx')
	if 'crop_offset_x' in options:
	    self.crop_offset[0] = self.config.getint(section, 'crop_offset_x')
	if 'crop_offset_y' in options:
	    self.crop_offset[1] = self.config.getint(section, 'crop_offset_y')
	if 'crop_w' in options:
	    self.crop_size[0] = self.config.getint(section, 'crop_w')
	if 'crop_h' in options:
	    self.crop_size[1] = self.config.getint(section, 'crop_h')
	if 'brackets' in options:
	    self.brackets = self.config.getboolean(section, 'brackets')
	if 'grayscale' in options:
	    self.show_gray = self.config.getboolean(section, 'grayscale')
	if 'ave_steps_fd' in options:
	    self.ave_steps_fd = self.config.getint(section, 'ave_steps_fd')
	else:
	    self.ave_steps_fd = 300
	if 'ave_steps_bk' in options:
	    self.ave_steps_bk = self.config.getint(section, 'ave_steps_bk')
	else:
	    self.ave_steps_bk = 300
	if 'pixels_per_step' in options:
	    self.pixels_per_step = self.config.getfloat(section, 'pixels_per_step')
	else:
	    self.pixels_per_step = 4.0
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

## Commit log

2014-06-17 mod stepper control
2014-06-17 optimise stepper control
2014-06-26 tweak camera settings
2014-07-07 add revised camera and lens mount
    [camera-mount-3.fcstd, camera-mount3.stl]
